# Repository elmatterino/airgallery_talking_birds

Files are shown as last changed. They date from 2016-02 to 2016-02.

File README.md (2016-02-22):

# AIR Gallery Talking Birds

The [Air Gallery](http://airgallery.net) in Portland, OR has a flock of
blackbirds as mascots. For the February 2016 show the director, Fred Swan,
wanted the blackbirds to greet visitors as they entered the gallery. This
project is a simple device that detects someone approaching the display,
greeting them with a chirp and special welcome message from one of the
resident artists.

## Bill of Materials

Except for the Arduino 101 and cigar box, I purchased all of the parts from
[Adafruit](https://www.adafruit.com/).

* [Arduino 101](https://www.arduino.cc/en/Main/ArduinoBoard101)
  * The Arduino Uno should be compatible with these instructions; though
    you will want to be sure to account for power differences.
* [Sharp GP2Y0A21YK0F IR distance sensor w/cable](https://www.adafruit.com/products/164)
* [Adafruit Audio FX Mini Sound Board - 2MB](https://www.adafruit.com/products/2342)
* [Adafruit Mono 2.5W Class D Audio Amplifier](https://www.adafruit.com/products/2130)
* [3" Speaker](https://www.adafruit.com/products/1314)
* [Adafruit Perma-Proto Half-sized Breadboard PCB](https://www.adafruit.com/products/1609)
* 4.7uF capacitor
* USB A to B cable
* 5V 1A USB wall adapter
* Cigar box
  * Check your local store with a humidor. They will likely have empty
    boxes you can buy for a few dollars.
* (optional) [3" male/male jumper wires](https://www.adafruit.com/products/759)
* (optional) [6" male/male jumper wires](https://www.adafruit.com/products/1957)

## Assembly

These instructions assemble a circuit that matches this diagram.
wiring diagram Wiring Diagram

* Connect 5V and GND from the Arduino 101 to the power rails on the perma-
  proto board.
* Solder the pins onto the audio board and amplifier
* Choose a location on the perma-proto board for the amplifier and audio
  board and solder the following pins to the perma-proto board
  * Amplifier: Vin, Gnd, A+, A-
  * Sound Board: Vin, Gnd, TX, RX, UG, R, Gnd (paired with R), Rst, Act
* Connect 5V rail to Vin on sound board and amplifier
* Connect GND rail to Gnd (paired with Vin) and UG on the sound board and
  Gnd on the amplifier
* Connect R and Gnd (paired with R) on the sound board to A+ and A- on the
  amplifier, respectively
* Connect TX and RX on the sound board to RX (pin 0) and TX (pin 1) on the
  Arduino 101, respectively
* Connect Rst on the sound board to pin 4 on the Arduino 101
* Connect Act on the sound board to pin 5 on the Arduino 101
* Choose two traces on the perma-proto board as 5V and GND to connect the
  distance sensor and connect the 5V and GND rails
* Connect the capacitor across the traces, making sure the positive lead is
  connected to the 5V trace
* Connect the red and black wires from the distance sensor to the 5V and
  GND traces next to the capacitor
* Connect the white wire from the distance sensor to pin A0 on the
  Arduino 101
* Print the
  [board stand](3d_parts/arduino_101_adafruit_half_perma_proto_stand.stl)
  and attach the Arduino 101 and perma-proto board
  * You may need to use a knife to open up the inside of the post caps,
    depending on your printer.

* Print the [distance sensor flange](3d_parts/dist_sensor_flange.stl)
* Cut a hole in the front of the cigar box to fit the sensor flange snug
* Drill a 3/4" hole in the back of the cigar box for the USB power cable
* Use a 3" hole saw to make a hole in the top of the box for the speaker
* Attach the speaker to the box over the hole
* Insert the distance sensor into the flange from inside the cigar box
  * You might need to chisel out some wood below the flange to make room
    for ther terminal block on the bottom of the sensor
* Attach the speaker to the terminal block on the amplifier
* Insert the USB cable through the hole in the back of the box
* Print the [cable hole plug](3d_parts/rear_plug.stl) (two halves), clamp
  over the USB cable and insert from the outside to seal the hole.

## Installing the Software

The project requires the
[Arduino IDE](https://www.arduino.cc/en/Main/Software) and the
[Adafruit Sound Board library](https://github.com/adafruit/Adafruit_Soundboard_library).
Installing the sound board library can be done by checking cloning a copy
from github into the Arduino library directory. On OS X, that directory is
/Users/__username__/Documents/Arduino/libraries.

```
cd ~/Documents/Arduino/libraries
git clone https://github.com/adafruit/Adafruit_Soundboard_library.git
```

## Adding Audio

There are two groups of audio files used by the project: chirps and
welcome messages. There can be up to MAX_SOUNDS in each group. If there are
more than MAX_SOUNDS files that would be part of a group, the extras are
ignored.

The chirp files contain the sounds the bird makes whenever it chirps. A
random chirp file is chosen whenever one is played. The files should be WAV
format, not OGG. The audio board does not signal on the Act pin properly
for OGG files, and it is important for this pin to have a correct signal
for proper operation of the device. I used 16 bit mono audio at 22500Hz to
save space. The file names must start with "CHIRP" (case insensitive) to be
part of this group.

The welcome messages play after the first chirp. A random message is played
whenever one is played. The files can be WAV or OGG, since a reliable
signal on Act is not required. I used Mono audio at 22500Hz in OGG format
to fit all of the artist's messages into the 2MB space.

To load the audio onto the audio board:
1. Make sure the USB cable is **NOT** connected to the Arduino 101
2. Connect your computer to the USB port on the audio board. A USB storage
   device will connect to your computer
3. Copy the audio files to the device
4. Safely eject the audio device USB storage. Watch for the drive to
   disconnect and remove the USB connection quickly, or else the device
   will reconnect to the computer

**IMPORTANT** Never have USB connected to the audio board and the
Arduino 101 at the same time. You could destroy the Arduino 101, the audio
board, or both if power is connected to both USB ports at the same time.

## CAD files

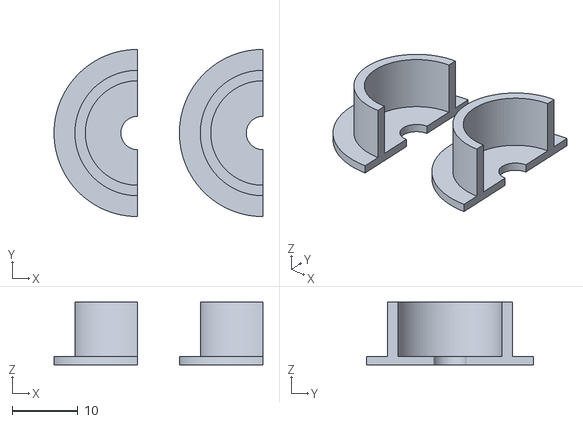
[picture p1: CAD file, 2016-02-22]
3d_parts/rear_plug.stl
31.8 x 25.4 x 9.52

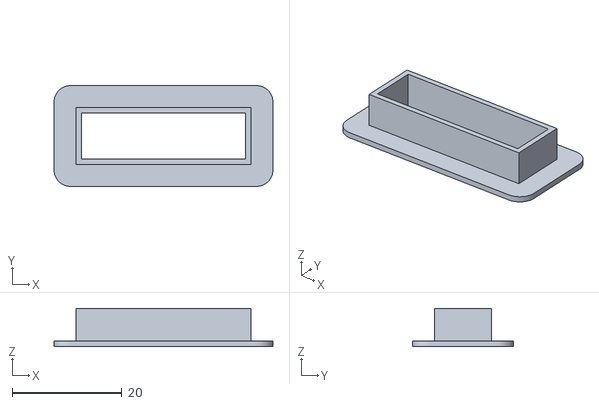
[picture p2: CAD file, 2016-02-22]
3d_parts/dist_sensor_flange.stl
40.0 x 18.4 x 7.00

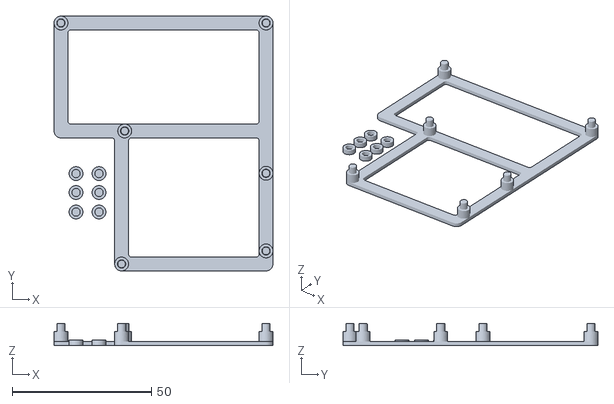
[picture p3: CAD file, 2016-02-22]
3d_parts/arduino_101_adafruit_half_perma_proto_stand.stl
78.7 x 91.6 x 8.00

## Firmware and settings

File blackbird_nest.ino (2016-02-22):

/*-------------------------------------------------------------------------
 * Copyright 2016 Matthew Wood
 *
 * Licensed under the Apache License, Version 2.0 (the "License");
 * you may not use this file except in compliance with the License.
 * You may obtain a copy of the License at
 *
 *     http://www.apache.org/licenses/LICENSE-2.0
 *
 * Unless required by applicable law or agreed to in writing, software
 * distributed under the License is distributed on an "AS IS" BASIS,
 * WITHOUT WARRANTIES OR CONDITIONS OF ANY KIND, either express or implied.
 * See the License for the specific language governing permissions and
 * limitations under the License.
 *-------------------------------------------------------------------------
 */
// Designed to run on an Arduino 101, but should be Arduino Uno compatible

#include <Adafruit_Soundboard.h>

//#define DEBUG_MODE  1
//#define VERBOSE_DEBUG_MODE 1

// Connect to output signal of distance sensor
#define PROXIMITY_SENSOR_PIN A0
// Connect to the RST pin on the Sound Board
#define SFX_RST 4
// Connect to the ACT pin on the Sound Board
#define SFX_ACT 5
// Connect to LED positive
#define LED     7

typedef enum {
  NOTHING,
  SOMETHING
} DistanceRange;

// Sensor value indicating the something in range (~90-100cm)
#define IN_RANGE_START  150

// Sound pattern when sensor picks up something in-range
// chirp -> welcome -> chirp x CHIRPS_PER_WELCOME -> repeat

// Milliseconds between samples
#define SAMPLE_TIME 500
// Milliseconds to pause between two chirps
#define CHIRP_PAUSE (120 * 1000)
// How many time to chirp between welcome messages
#define CHIRPS_PER_WELCOME 5

// Pass the Serial1 interface (pins 1&2 on Arduino 101) to
// Adafruit_Soundboard, the second argument should be NULL, and the third
// arg is the reset pin
Adafruit_Soundboard sfx = Adafruit_Soundboard(&Serial1, NULL, SFX_RST);

// Support up to MAX_SOUNDS chirping sounds and MAX_SOUNDS welcome messages
// Files containing chirp sounds must start with CHIRP_SOUND_PREFIX (case
// insensitive). Files containing welcome sound must start with
// WELCOME_SOUND_PREFIX (case insensitive).
#define MAX_SOUNDS  16
#define CHIRP_SOUND_PREFIX "CHIRP"
#define WELCOME_SOUND_PREFIX "WELC"
int num_chirp_sounds = 0;
int chirp_sounds[MAX_SOUNDS];
int num_welcome_sounds = 0;
int welcome_sounds[MAX_SOUNDS];

void setup() {
  // Open serial communications and wait for port to open
  Serial.begin(115200);
#ifdef DEBUG_MODE
  while (!Serial) {
    ; // wait for serial port to connect.
  }
#endif

  pinMode(LED, OUTPUT);
  
  Serial1.begin(9600); // AudioFX boards use 9600 baud
  while (!Serial1) {
    ; // wait for serial port to connect.
  }
  Serial.println("Starting");

  // Initialize the comms with the audio board on serial
  pinMode(SFX_ACT, INPUT);
  if (!sfx.reset()) {
    Serial.println("Not found");
    while (1);
  }
  Serial.println("SFX board found");
  
  // Discover the set of audio files to use
  uint8_t files = sfx.listFiles();
  Serial.println("File Listing");
  Serial.println("========================");
  Serial.println();
  Serial.print("Found "); Serial.print(files); Serial.println(" Files");
  for (uint8_t f = 0; f < files; f++) {
    Serial.print(f);
    Serial.print("\tname: "); Serial.print(sfx.fileName(f));
    Serial.print("\tsize: "); Serial.println(sfx.fileSize(f));
    if (strstr(sfx.fileName(f), CHIRP_SOUND_PREFIX) == sfx.fileName(f)) {
      Serial.println("chirp sound found");
      chirp_sounds[num_chirp_sounds++] = f;
    }
    else if (strstr(sfx.fileName(f), WELCOME_SOUND_PREFIX) == sfx.fileName(f)) {
      Serial.println("welcome sound found");
      welcome_sounds[num_welcome_sounds++] = f;
    }
  }
  Serial.println("========================");

  // Seed the PRNG from noise in the sensor
  srand(rand() + analogRead(PROXIMITY_SENSOR_PIN));
}

int getFilteredSensorValue() {
  // The sensor is somewhat noisy. Keep a circular buffer and use the average.
#define NUM_SENSOR_VALUES 3
  static int index = 0;
  static int sensorValues[NUM_SENSOR_VALUES] = {0};
  
  // read the value from the sensor:
  sensorValues[index] = analogRead(PROXIMITY_SENSOR_PIN);

  // update the random seed
  srand(rand() + sensorValues[index]);
  
  // get simple mean
  int sum = 0;
  for (int i = 0; i < NUM_SENSOR_VALUES; i++) {
    sum += sensorValues[i];
  }

#ifdef VERBOSE_DEBUG_MODE
  for (int i = 0; i < NUM_SENSOR_VALUES; i++) {
    Serial.print(sensorValues[i]);
    Serial.print(" ");
  }
  Serial.println("");
#endif

  index = (index + 1) % NUM_SENSOR_VALUES;
  return sum / NUM_SENSOR_VALUES;
}

DistanceRange getDistanceRange(int sensor_value) {
  if (sensor_value >= IN_RANGE_START) {
    return SOMETHING;
  }
  return NOTHING;
}

DistanceRange last_distance = NOTHING;
int chirp_count = 0;
int chirps_remaining = 0;
boolean welcome_msg = false;
unsigned pause_time = 0;
unsigned pause_time_remaining = 0;

void setNothingState() {
  chirp_count = 0;
  chirps_remaining = 0;
  welcome_msg = false;
  pause_time = 0;
  pause_time_remaining = 0;  
}

void setSomethingState() {
  chirp_count = CHIRPS_PER_WELCOME;
  chirps_remaining = (last_distance == NOTHING) ? 1 : 0;
  welcome_msg = true;
  pause_time = CHIRP_PAUSE;
  pause_time_remaining = 0;
}

void playSound(int id) {
  digitalWrite(LED, HIGH);
  
  if (sfx.playTrack(id)) {
    // While track plays, keep the sensor sampling running
    while (digitalRead(SFX_ACT) == LOW) {
      Serial.print(".");
      delay(SAMPLE_TIME);
      getFilteredSensorValue();
    }
    Serial.println("+");
  }
  else {
    Serial.println("!");
  }
  
  digitalWrite(LED, LOW);
}

void loop() {
  pause_time_remaining -= SAMPLE_TIME;
  
  // Figure out if we should change state
  DistanceRange distance = getDistanceRange(getFilteredSensorValue());
  if (last_distance != distance) {
    switch (distance) {
    case NOTHING:
      setNothingState();
      break;
    case SOMETHING:
      setSomethingState();
      break;
    }
  }

  // Play a sound, if appropriate
  if (pause_time_remaining == 0 && pause_time > 0) {
    if (chirps_remaining-- >= 0) {
      Serial.println("chirp");
      playSound(chirp_sounds[rand() % num_chirp_sounds]);
    }
    if (chirps_remaining == 0 && welcome_msg) {
      // Make sure the person is still there after the first chirp
      if (getDistanceRange(getFilteredSensorValue()) != NOTHING) {
        Serial.println("welcome");
        playSound(welcome_sounds[rand() % num_welcome_sounds]);
      }
    }

    // reset the chirp count
    if (chirps_remaining < 0) {
      chirps_remaining = chirp_count;
    }

    pause_time_remaining = pause_time;
  }

  last_distance = distance;
#ifdef DEBUG_MODE
  Serial.print("ld: ");
  Serial.print(last_distance);
  Serial.print(" cc: ");
  Serial.print(chirp_count);
  Serial.print(" cr: ");
  Serial.print(chirps_remaining);
  Serial.print(" wm: ");
  Serial.print(welcome_msg);
  Serial.print(" pt: ");
  Serial.print(pause_time);
  Serial.print(" ptr: ");
  Serial.println(pause_time_remaining);
#endif
  delay(SAMPLE_TIME);
}
